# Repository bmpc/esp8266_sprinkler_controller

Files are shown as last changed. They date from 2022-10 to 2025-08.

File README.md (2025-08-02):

# ESP8266 sprinkler controller
 
A WiFi lawn irrigation controller using an [ESP-12F WiFi module](https://docs.ai-thinker.com/_media/esp8266/docs/esp-12f_product_specification_en.pdf) to drive up to 4 sprinkler stations.
 
The sprinkler stations can be controlled and programmed remotely using [Home Assistant](https://www.home-assistant.io/).
 
The ESP8266 board communicates with Home Assistant using an [MQTT](https://mqtt.org/) broker on the local WiFi network. The ESP8266 listens to events in order to turn on/off and to program the schedule for each sprinkler station.
 
The controller is powered by a 9V battery as this is also the voltage required to activate the solenoids for each sprinkler. Being a battery powered device, the efficiency of the circuit is very important. The ESP8266 needs to be in deep sleep as much as possible and only wake up for activating/deactivating sprinkler stations.
 
There is also an interface mode that can be activated explicitly using Home Assistant. In interface mode, the ESP8266 will not go into deep sleep and is always ready to receive commands to activate/deactivate stations and configure the system. This mode is useful if we need to test a specific sprinkler station or if we need to trigger the stations manually.
 
The controller is also equipped with a reset button which will force the system to wake up from deep sleep, and go into interface mode (if enabled).
 
<div style="text-align:center">
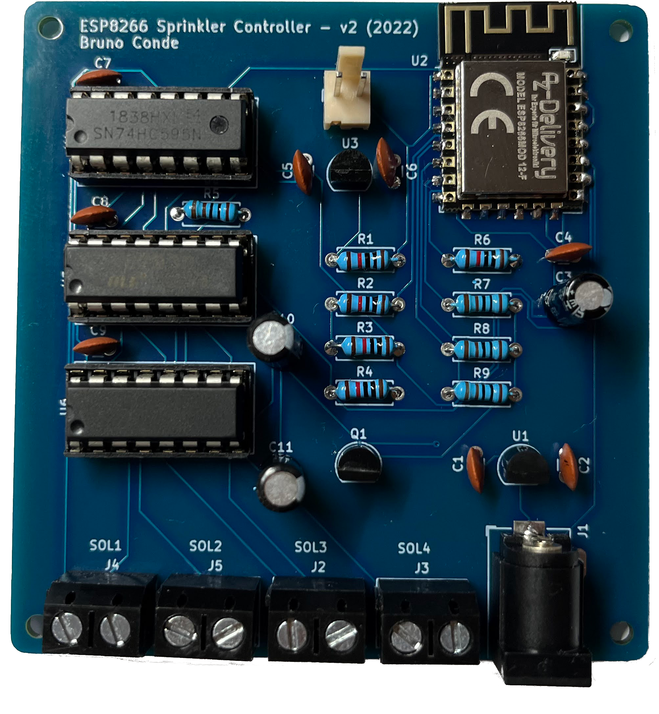
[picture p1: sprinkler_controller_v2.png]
Controller circuit
 
</div>
 
## MQTT Topics
 
### Subscribe
 
| Topic | Payload format | Payload example | Retained |
| --- | --- | --- | --- |
| `lawn-irrigation/station{x}/set` | `{"on","off"}\|{"duration in milliseconds"}` | `"on\|18000" ; "off"` | false |
| `lawn-irrigation/station{x}/config`  | `{"cron expression"}\|{"duration in milliseconds"}` | `"0 30 6 1-31/2 * *\|900"` | true |
| `lawn-irrigation/interface-mode/set` | `{"on","off"}` | `"on" ; "off"` | true |
| `lawn-irrigation/enabled/set` | `{"on","off"}` | `"on" ; "off"` | true |

### Publish
 
| Topic | Payload format | Payload example | Retained |
| --- | --- | --- | --- |
| `lawn-irrigation/station{x}/state` | `{"on","off"}` | `"on" ; "off"`  | false |
| `lawn-irrigation/interface-mode/state`  | `{"on","off"}` | `"on" ; "off"`  | false |
| `lawn-irrigation/log` |  `<string>` | `"log string"`  | true |
 
## How to configure Home Assistant
 
The esp8266 sprinkler controller is configured from [Home Assistant](https://www.home-assistant.io/) using [MQTT switches](https://www.home-assistant.io/integrations/switch.mqtt/) and input fields.
 
As an example, here is my lawn irrigation card within the Home Assistant dashboard. I have three sprinkler stations configured:
 
<div style="text-align:center">
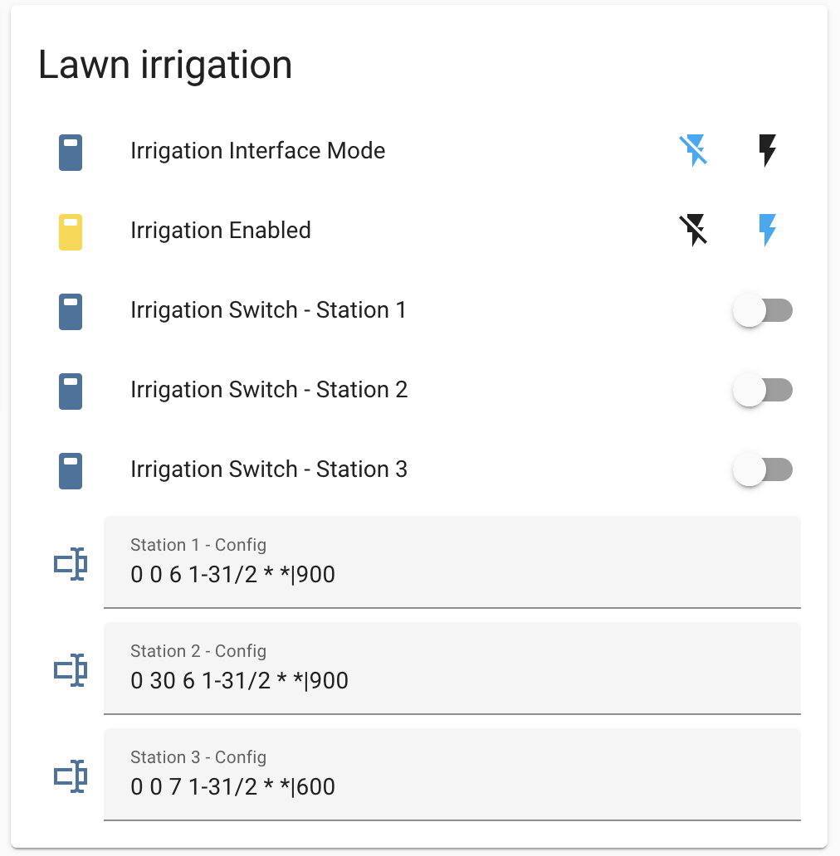
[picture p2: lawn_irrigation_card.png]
Home Assistant control card
 
</div>
 
Each station is controlled by a different MQTT switch. The switches automatically display the station state and are also used to trigger the stations manually (provided that the controller is in **interface mode**).
 
Besides the station controller switches and CRON inputs, there are two additional switches to toggle:
- the interface mode
- the irrigation itself.
 When the irrigation controller is in **interface mode**, the ESP8266 will not go into deep sleep and the user can toggle the stations directly.
 
The irrigation toggle switch can be used to skip the programmed schedule. As an example, it is possible to disable the irrigation if rain is forecast for the next 12 hours or is has rained in the last 12h.
 
Apart from the switches, [Input Text Fields](https://www.home-assistant.io/integrations/input_text/) are used to configure the CRON expression and duration for each station. An automation is also required so that an MQTT event is published whenever the text field changes.
 
If a station is activated due to the configured cron expression schedule, the respective switch will be updated automatically with the current status as an MQTT event is sent from the controller whenever there is a station event.
 
You can find an example on how to configure these MQTT switches and text fields on the HA examples included in this repository:
- [configuration.yaml](/ha/configuration.yaml)
- [automations.yaml](/ha/automations.yaml)

## Circuit
 
### Power
 
Because the solenoids that activate the sprinklers require 9V to activate, this circuit is powered by a 9V battery (two 9V batteries in parallel to be precise). A voltage regulator is used to step down from 9v to 5v so that we can power some 5v ICs in the circuit. The ESP-12F requires 3.3V. Therefore, another voltage regulator was added to step down from 5v to 3.3v. This is not ideal, as there are two voltage regulators but in this case we require 3 different voltages and it would not be practical to have multiple batteries for the same circuit.
 
### Latching solenoids and the L293D ICs
 
There are two L293D ICs in this circuit. These are Quadruple Half-H Drivers that are designed to provide bidirectional drive currents. The L293D is also designed to drive inductive loads such as solenoids and motors. These ICs allow us to drive the 9v power lines to the solenoid with a 3.3v logic signal provided by the ESP8266.
 
A latching solenoid uses an electrical current pulse or internal permanent magnet material to maintain a set position without the constant application of power. Latching solenoids (also known as bistable solenoids) have two standard positions; de-energized with the plunger fully extended and de-energized with the plunger held in position by permanent magnets.
 
Electrical polarity is vital to proper latching a solenoid. As current flows in one direction, adds to the pull of the permanent magnet. Sending a current through the coil field in the opposite direction cancels the magnet’s attraction and releases the plunger from the latched position.
 
These L293D ICs are required in order to control our latching solenoids because we need to provide opposite polarities depending on if we are activating or deactivating the solenoid.
 
Each L293D can control two solenoids. Hence two L293D ICs were used to drive a total of 4 solenoids/sprinkler stations.
 
### The lack of pins and the 8-bit shift register
 
Because the ESP12-F only provides 11 GPIO digital pins, an 8-bit shift register was included so we can have more digital lines to drive the four possible solenoids/stations.
 
### Power Efficiency
 
This is a very important topic as this circuit is powered with standard 9v batteries. Depending on the battery type, usually a 9v battery has a capacity of around 300 mAh.
We must guarantee that our circuit is as efficient as possible. Ideally, the standby current of the circuit should not exceed 50uA. In these conditions, I estimate around 300 to 400 days on double 9v batteries.
 
Operating normally, without any changes to improve the efficiency of the circuit, the average current is about 90mA to 130mA. This includes the ESP8266 making WiFi requests, the two L293D ICs, the 8-bit shift register, and added the voltage regulators.
 
If we put the ESP8266 in deep sleep mode, the current drops to about 50mA to 60mA. This is still too high. The culprits are the two L293D ICs which have a very high quiescent current of about 30mA each.
 
Hence, to reduce the quiescent current of the L293D ICs, the power is supplied to these ICs only when stations need to be activated/deactivated. To achieve this, a simple NPN transistor is used to turn off the shift register and both L293D ICs. This transistor is driven by the ESP8266.
 
Even though the L293D ICs are not connected to power in standby mode, some pins can have enough voltage to pull the ESP-12F GPIO15 line HIGH thus preventing the ESP-12F from booting. The solution was to add a diode between the GPIO15 enable line and the L293D chip.
 
After these improvements, I measured the standby current of the circuit to around **20uA**.

### RTC accuracy on the ESP8266 

The max deep sleep time of the ESP-12F is about 3 to 4 hours. Therefore, the ESP needs to wake up every 3 hours or so and get right back to sleep if no action is required (no station needs to be started or stopped).

Also, it turns out that the ESP8266 doesn't have a very precise RTC (Real Time Clock). On a 3 hour period, my ESP8266 RTC would drift ahead around 14 minutes. Without a more precise clock, and considering our use case, we can just go back to sleep for the remaining time. 
 
### Schematic
 
<div style="text-align:center">
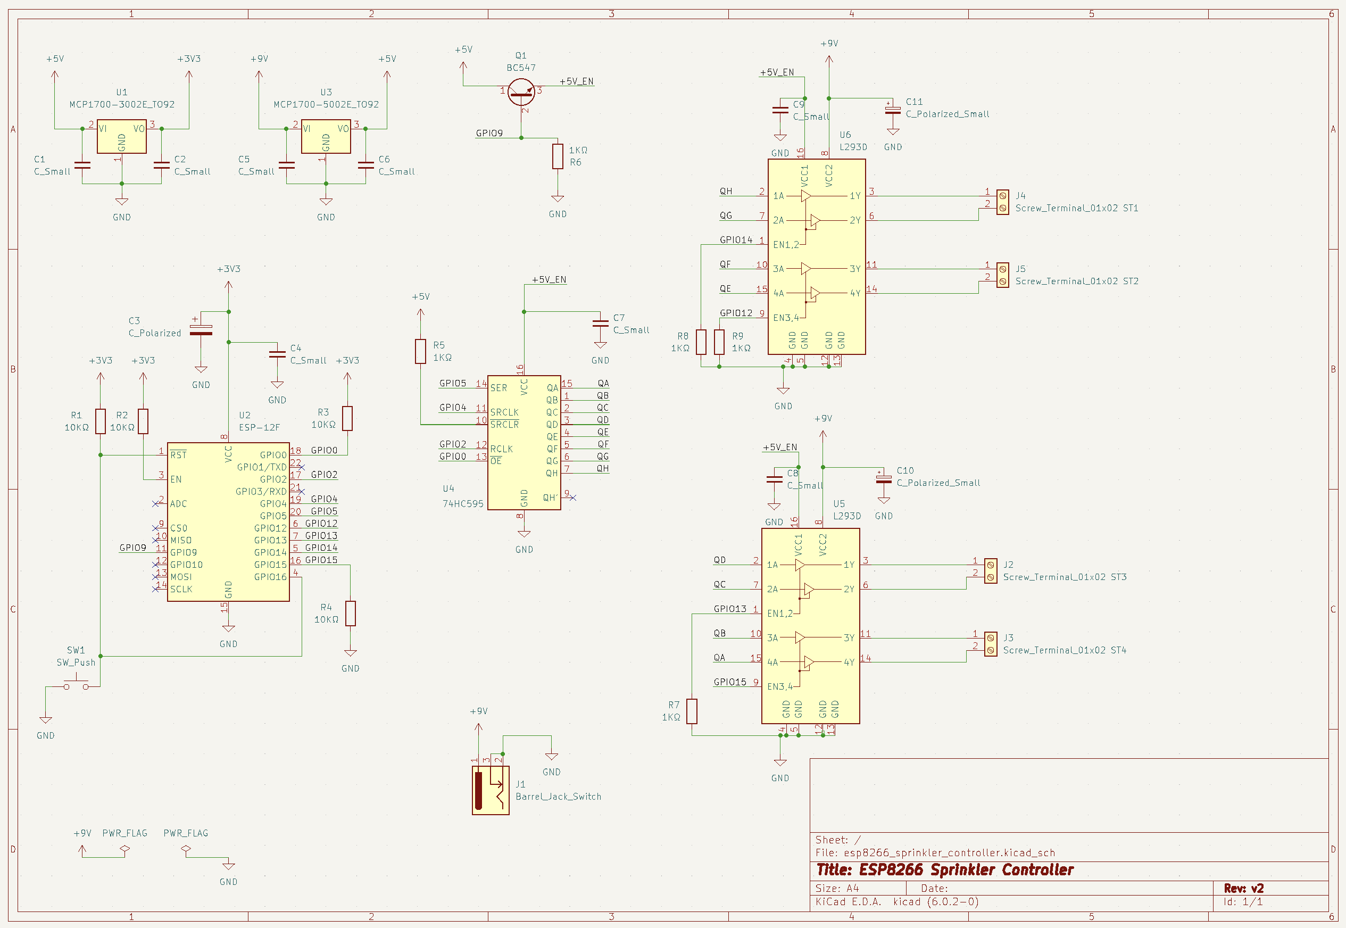
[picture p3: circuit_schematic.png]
Circuit Schematic
 
</div>
 
### BOM

| Part | Qty |
| --- | --- |
| ESP-12F (ESP8266) | x1  |
| L293D (Quadruple Half-H Drivers) | x2  |
| 74HC595 (8-bit shift register) | x1  |
| MCP1702-5002E/TO (voltage regulator) | x1  |
| MCP1702-3302E/TO (voltage regulator) | x1  |
| SS8050CBU (NPN transistor) | x1  |
| 100Ω resistor | x1  |
| 1k resistor | x4  |
| 10k resistor | x4  |
| 100 uF electrolytic capacitor | x2  |
| 10 uF electrolytic capacitor | x1  |
| 1 uF ceramic capacitor (104) | x8  |
| SD101A (Schottky Diode) | x1  |
| Switch (reset) | x1  |
| Barrel Jack Switch | x1  |
| Screw terminal | x4  |
| 9v battery | x2  |
| Rainbird solenoids | x3  |

## ESP8266 Project

The ESP8266 project was built using [Platform IO](https://docs.platformio.org/).

The platformio.ini file contains the default parameters to run the targets below. You can change this file or provide the parameters in the context of each `pio run <target>` command [(usage)](https://docs.platformio.org/en/latest/core/userguide/cmd_run.html#usage).

### Build

In order to compile and build the project you just need to run the following command.

`pio run build`

### Upload

You can upload the sketch using serial port or OTA (Over The Air).

The sketch is ready to receive (OTA) updates. In order to upload OTA, you need to set the `upload_port` parameter with the IP address or your ESP8266.
For serial upload, just se the `upload_port` parameter with the appropriate serial interface.

`pio run upload`

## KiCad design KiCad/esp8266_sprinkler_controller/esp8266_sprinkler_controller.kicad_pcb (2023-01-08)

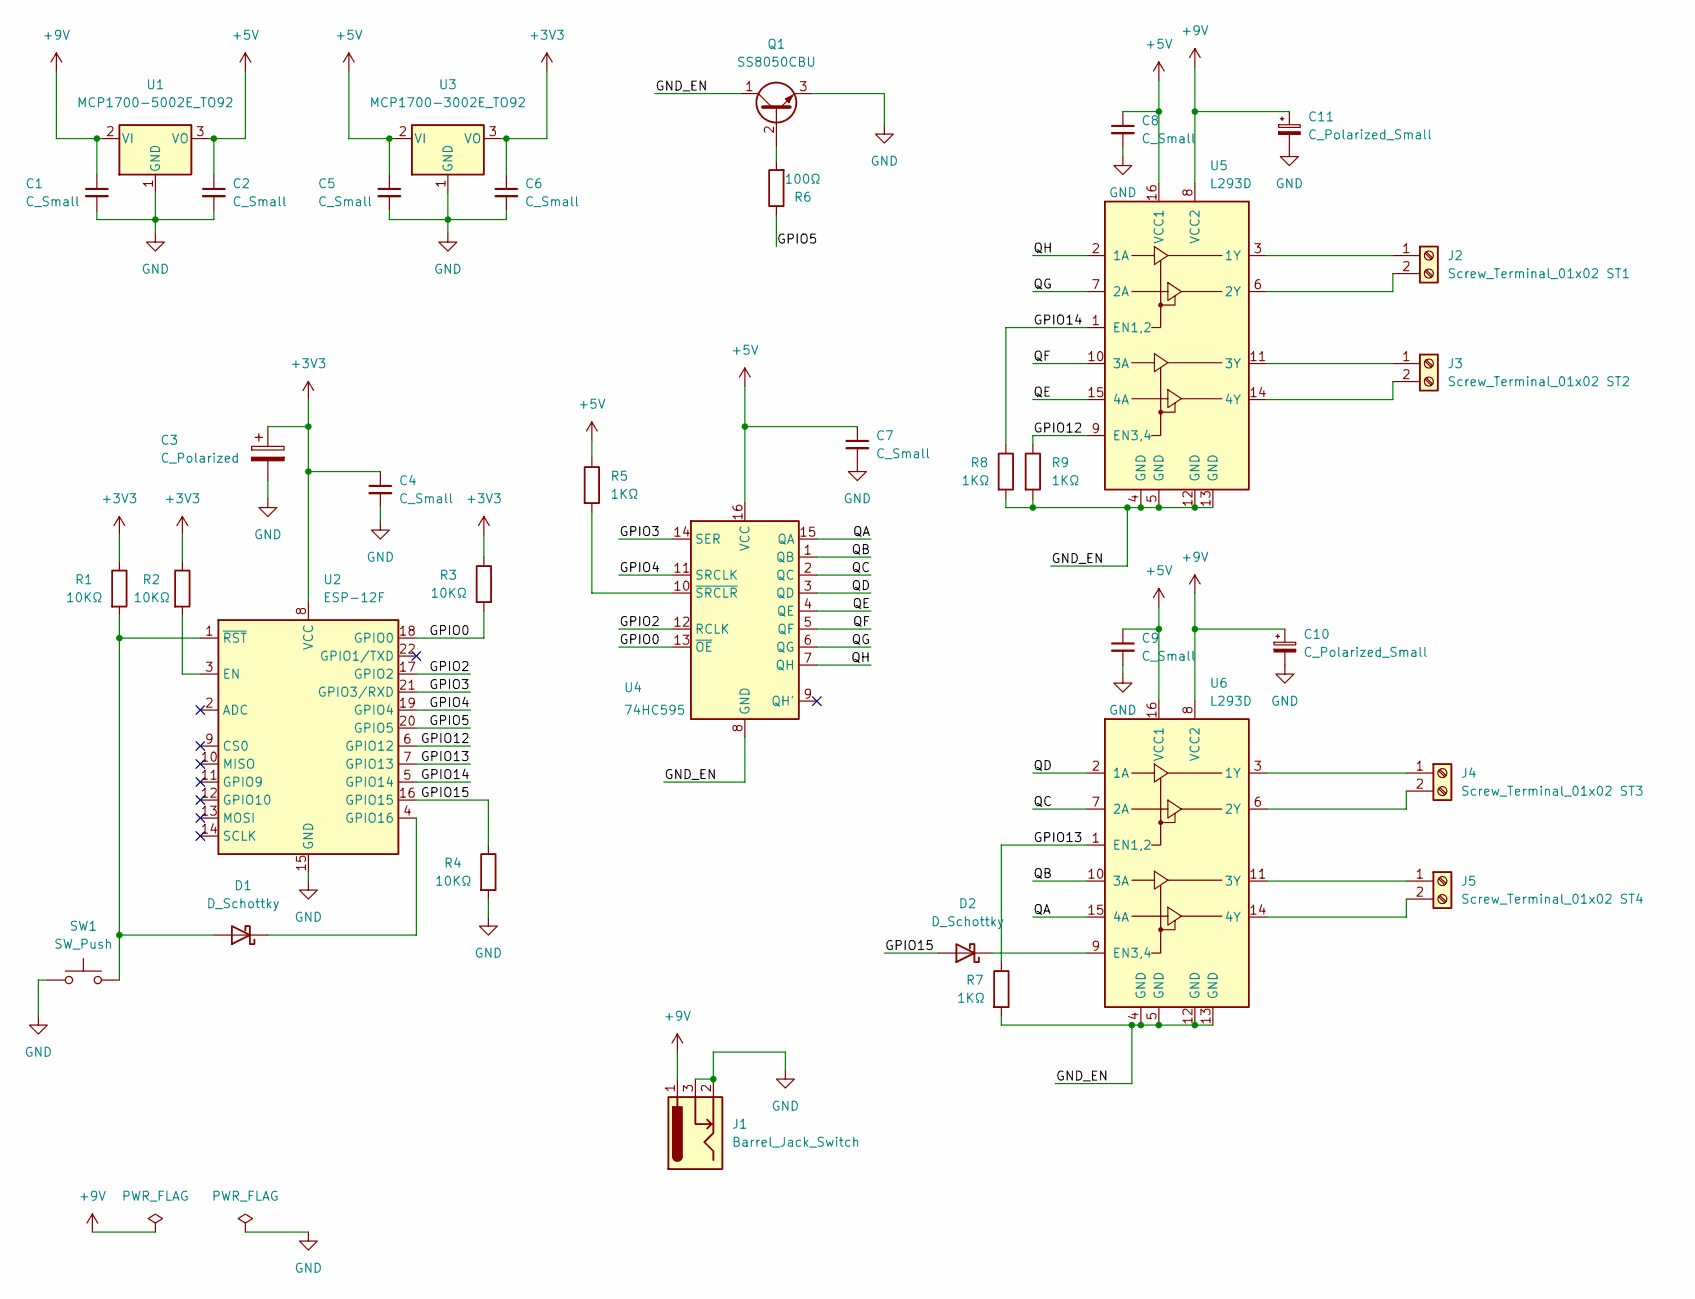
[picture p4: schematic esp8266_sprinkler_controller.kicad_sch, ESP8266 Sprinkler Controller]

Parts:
C1, C2, C4, C5, C6, C7, C8, C9: C_Small; C_Disc_D3.0mm_W1.6mm_P2.50mm
C3: C_Polarized; CP_Radial_D4.0mm_P2.00mm
C10, C11: C_Polarized_Small; CP_Radial_D4.0mm_P2.00mm
D1, D2: D_Schottky; D_A-405_P7.62mm_Horizontal
J1: Barrel_Jack_Switch; BarrelJack_Horizontal
J2: Screw_Terminal_01x02 ST1; TerminalBlock_bornier-2_P5.08mm
J3: Screw_Terminal_01x02 ST2; TerminalBlock_bornier-2_P5.08mm
J4: Screw_Terminal_01x02 ST3; TerminalBlock_bornier-2_P5.08mm
J5: Screw_Terminal_01x02 ST4; TerminalBlock_bornier-2_P5.08mm
Q1: SS8050CBU; TO-92
R1, R2, R3, R4: 10KΩ; R_Axial_DIN0207_L6.3mm_D2.5mm_P7.62mm_Horizontal
R5, R7, R8, R9: 1KΩ; R_Axial_DIN0207_L6.3mm_D2.5mm_P7.62mm_Horizontal
R6: 100Ω; R_Axial_DIN0207_L6.3mm_D2.5mm_P7.62mm_Horizontal
SW1: SW_Push; PinSocket_1x02_P2.54mm_Vertical
U1: MCP1700-5002E_TO92; TO-92
U2: ESP-12F; ESP-12E
U3: MCP1700-3002E_TO92; TO-92
U4: 74HC595; DIP-16_W7.62mm_Socket
U5, U6: L293D; DIP-16_W7.62mm_Socket

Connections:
+3V3: C3.1, C4.1, C6.1, R1.1, R2.1, R3.1, U2.8 (VCC), U3.3 (VO)
+5V: C2.1, C5.1, C7.1, C8.1, C9.1, R5.1, U1.3 (VO), U3.2 (VI), U4.16 (VCC), U5.16 (VCC1), U6.16 (VCC1)
+9V: C1.1, C10.1, C11.1, J1.1, U1.2 (VI), U5.8 (VCC2), U6.8 (VCC2)
/GND_EN: Q1.1 (C), R7.2, R8.2, R9.2, U4.8 (GND), U5.4 (GND), U5.5 (GND), U5.12 (GND), U5.13 (GND), U6.4 (GND), U6.5 (GND), U6.12 (GND), U6.13 (GND)
/GPIO0: R3.2, U2.18 (GPIO0), U4.13 (~OE)
/GPIO2: U2.17 (GPIO2), U4.12 (RCLK)
/GPIO3: U2.21 (GPIO3/RXD), U4.14 (SER)
/GPIO4: U2.19 (GPIO4), U4.11 (SRCLK)
/GPIO5: R6.1, U2.20 (GPIO5)
/GPIO12: R9.1, U2.6 (GPIO12), U5.9 (EN3,4)
/GPIO13: R7.1, U2.7 (GPIO13), U6.1 (EN1,2)
/GPIO14: R8.1, U2.5 (GPIO14), U5.1 (EN1,2)
/GPIO15: D2.2 (A), R4.1, U2.16 (GPIO15)
/QA: U4.15 (QA), U6.15 (4A)
/QB: U4.1 (QB), U6.10 (3A)
/QC: U4.2 (QC), U6.7 (2A)
/QD: U4.3 (QD), U6.2 (1A)
/QE: U4.4 (QE), U5.15 (4A)
/QF: U4.5 (QF), U5.10 (3A)
/QG: U4.6 (QG), U5.7 (2A)
/QH: U4.7 (QH), U5.2 (1A)
GND: C1.2, C2.2, C3.2, C4.2, C5.2, C6.2, C7.2, C8.2, C9.2, C10.2, C11.2, J1.2, J1.3, Q1.3 (E), R4.2, SW1.1, U1.1 (GND), U2.15 (GND), U3.1 (GND)
unnamed: D1.1 (K), U2.4 (GPIO16)
unnamed: D1.2 (A), R1.2, SW1.2, U2.1 (~RST)
unnamed: D2.1 (K), U6.9 (EN3,4)
unnamed: J2.1, U5.3 (1Y)
unnamed: J2.2, U5.6 (2Y)
unnamed: J3.1, U5.11 (3Y)
unnamed: J3.2, U5.14 (4Y)
unnamed: J4.1, U6.3 (1Y)
unnamed: J4.2, U6.6 (2Y)
unnamed: J5.1, U6.11 (3Y)
unnamed: J5.2, U6.14 (4Y)
unnamed: Q1.2 (B), R6.2
unnamed: R2.2, U2.3 (EN)
unnamed: R5.2, U4.10 (~SRCLR)

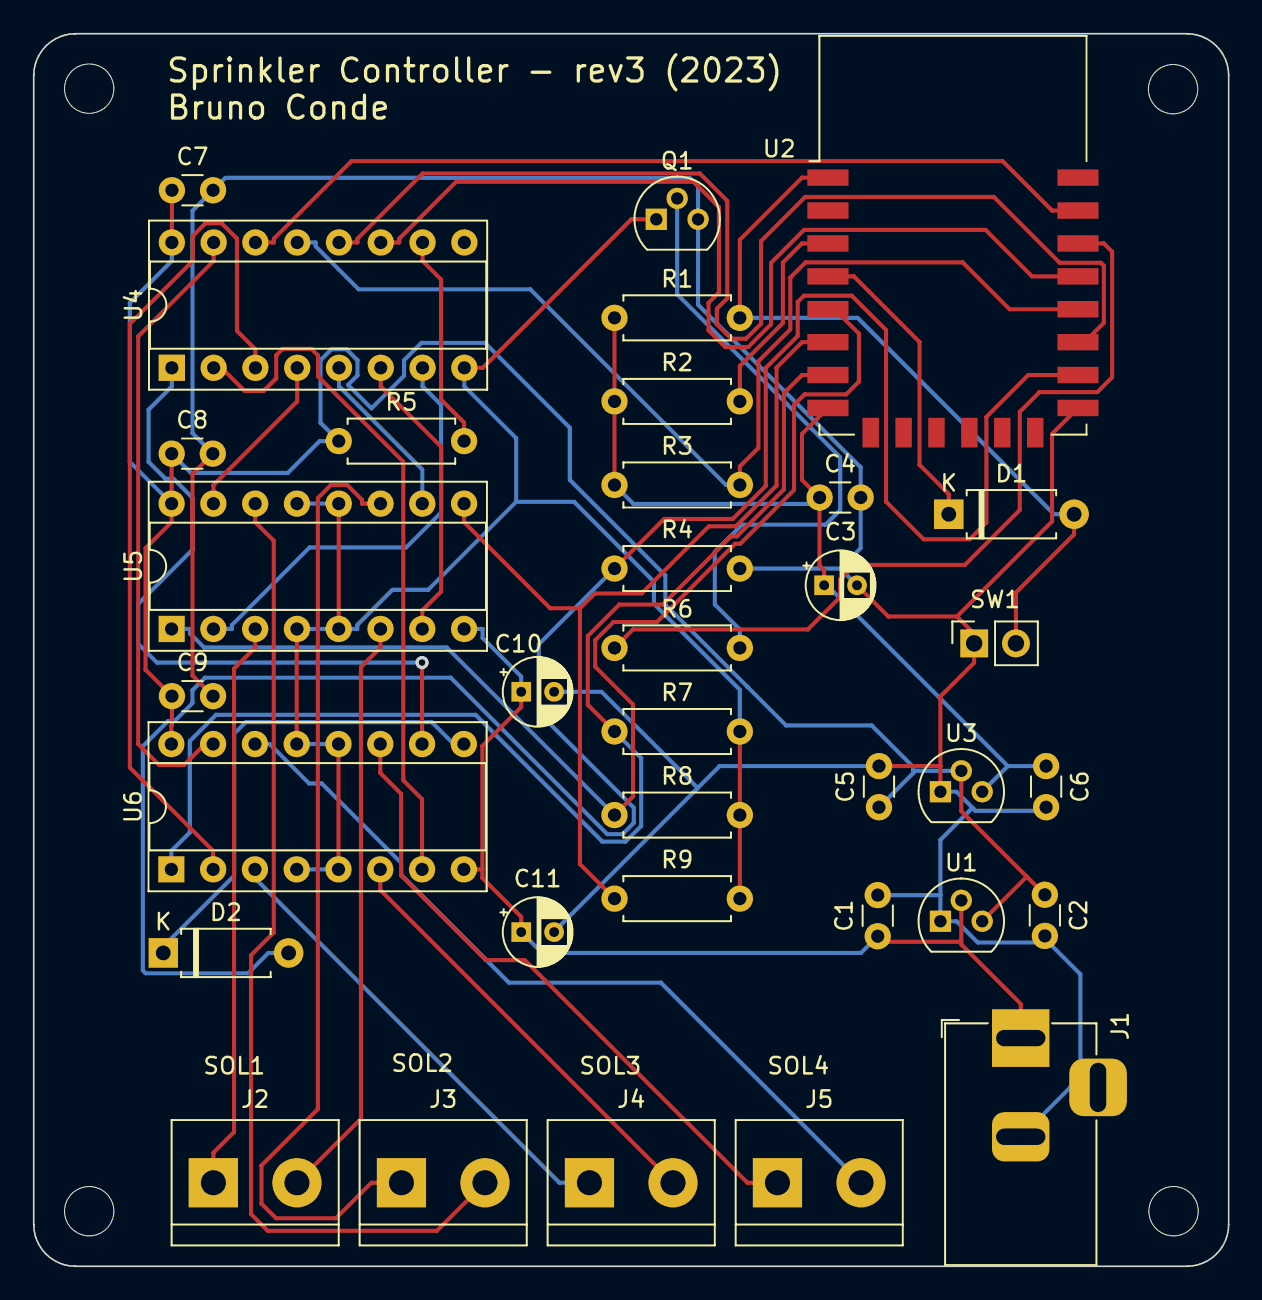
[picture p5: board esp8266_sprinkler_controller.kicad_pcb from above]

Board: 2 copper layers, 72.6 x 74.9 mm, 39 parts (0 on the bottom side), 36 nets.

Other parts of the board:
Hole1, Hole2, Hole3, Hole4: MountingHole_3mm

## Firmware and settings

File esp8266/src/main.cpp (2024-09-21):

/**
 * This is an esp8266 project to control a lawn irrigation system using
 * solanoids for each sprinkler station. It connects to an MQTT broker on the
 * local WiFi network so that it can listen for events to turn on/off each
 * sprinkler station on the irrigation system. 
 * 
 * The system has two functioning modes:
 *   1. Background - The default mode which triggers each station based on it's cron schedule.
 *   2. Interface  - An interactive mode where users can trigger specific stations from 
 *                   MQTT events (Usually used for ad-hoc watering or to test the spinklers).
 * 
 * The mode can be selected using an MQTT event. While on Background mode, the ESP8266 is 
 * in deep spleeping and a manual restart is required for the ESP8266 to restart and activate
 * the interface mode.
 * 
 * WARNING: While on interafce mode, the ESP8266 is always on. This will degrade the battery life much faster.
 * 
 * Stations are mutual exclusive. There can only be one station active at a time, which usually is the behavior of sprinkler irrigation systems.  
 * 
 * MQTT topics:
 *  Subsribe:
 *   - lawn-irrigation/station{x}/set     not retained -> payload: on|18000 ; off
 *   - lawn-irrigation/station{x}/config      retained -> payload: cron|18000
 *   - lawn-irrigation/interface-mode/set     retained -> payload: on ; off
 *   - lawn-irrigation/enabled/set            retained -> payload: on ; off
 * 
 *  Publish:
 *   - lawn-irrigation/station{x}/state
 *   - lawn-irrigation/interface-mode/state
 *   - lawn-irrigation/log
 *
 * @file main.cpp
 * @author Bruno Conde
 * @brief
 * @version 0.1
 * @date 2022-09-18
 *
 * @copyright Copyright (c) 2022
 *
 */

#include <Arduino.h>
#include <NTPClient.h>
#include <WiFiUdp.h>
#include <ArduinoOTA.h>

#include "mqttcli.h"
#include "stations.h"
#include "log.h"
#include "constants.h"

const int DEEP_SLEEP_THRESHOLD = 3 * 60 * 60; // 3 hours in seconds

using namespace sprinkler_controller;

StationController stctr;
WiFiUDP ntpUDP;
NTPClient time_client(ntpUDP);

void enter_deep_sleep() {
  // Find out the next event
  time_t now = time_client.getEpochTime();
  StationEvent ev = stctr.next_station_event();

  time_t sleep_duration = DEEP_SLEEP_THRESHOLD;
  if (ev.type != EventType::NOOP && ev.time > now) {
    time_t new_sleep_duration = ev.time - now;
    // The maximum deep sleep time is around 3 hours. This may vary due to temperature changes. 
    // ESP.deepSleepMax() provides the max deep sleep.
    // We wake up every 3 hours and go right back to sleep if no stations need to be started/stopped. 
    if (new_sleep_duration <= DEEP_SLEEP_THRESHOLD) {
      sleep_duration = new_sleep_duration;
    }

    char msg[200] = {0};
    ev.to_string(msg);
    report_log("[%lld] Next event: %s", now, msg);
  } else {
    // There isn't a next event to process
    report_log("[%lld] No next event found!", now);
  }

  report_log("[%lld] Entering deep sleep mode for '%lld' seconds... good night!", now, sleep_duration);

  mqttcli::disconnect();

  ESP.deepSleep(sleep_duration * 1000 * 1000); // convert from seconds to microseconds
}

void init_wifi() {
  delay(100);
  // We start by connecting to the WiFi network
  debug_printf("Connecting to %s\n", SSID);

  WiFi.setAutoConnect(true);
  WiFi.setAutoReconnect(true);

  WiFi.begin(SSID, PASSWORD);

  while (WiFi.status() != WL_CONNECTED) {
    debug_printf(".");
    delay(500);
  }

  randomSeed(micros());

  debug_printf("WiFi connected. IP address: %s\n", WiFi.localIP().toString().c_str());
}

void setup() {  
  setupSerial();

  init_wifi();
  time_client.begin();

  stctr.init(&time_client);

  if (!stctr.is_interface_mode()) {
    stctr.process_station_event();
    enter_deep_sleep();
  }

  ArduinoOTA.onStart([]() {
    String type;
    if (ArduinoOTA.getCommand() == U_FLASH) {
      type = "sketch";
    } else { // U_FS
      type = "filesystem";
    }

    // NOTE: if updating FS this would be the place to unmount FS using FS.end()
    debug_printf("Start updating %s\n", type);
  });
  ArduinoOTA.onEnd([]() {
    debug_printf("\nEnd");
  });
  ArduinoOTA.onProgress([](unsigned int progress, unsigned int total) {
    debug_printf("Progress: %u%%\r", (progress / (total / 100)));
  });
  ArduinoOTA.onError([](ota_error_t error) {
    debug_printf("Error[%u]: ", error);
    if (error == OTA_AUTH_ERROR) {
      debug_printf("Auth Failed");
    } else if (error == OTA_BEGIN_ERROR) {
      debug_printf("Begin Failed");
    } else if (error == OTA_CONNECT_ERROR) {
      debug_printf("Connect Failed");
    } else if (error == OTA_RECEIVE_ERROR) {
      debug_printf("Receive Failed");
    } else if (error == OTA_END_ERROR) {
      debug_printf("End Failed");
    }
    debug_printf("\n");
  });
  ArduinoOTA.begin();
}

void loop() {
  if (!stctr.is_interface_mode()) {
    debug_printf("Interface mode switched off.");
    // if we get here, this means that the interface mode was switched off
    stctr.check_stop_stations(true);
    enter_deep_sleep();
  }

  if (WiFi.status() != WL_CONNECTED) {
    Serial.println("WiFi disconnected. Reconnecting...");
    WiFi.reconnect();
    
    while (WiFi.status() != WL_CONNECTED) {
      debug_printf(".");
      delay(500);
    }

    stctr.init(&time_client);
  }

  ArduinoOTA.handle();

  stctr.loop();
  
}

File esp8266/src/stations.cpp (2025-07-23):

#include "stations.h"
#include "ccronexpr/ccronexpr.h"
#include "log.h"
#include <EEPROM.h>

namespace sprinkler_controller {

static uint8_t EEPROM_MARKER = 115;

static int EEPROM_SIZE = sizeof(EEPROM_MARKER) + sizeof(StationEvent) + (sizeof(Station) * NUM_STATIONS);

static uint64_t lastMillis = 0;

// topics to subscribe 
const char *SUBS_TOPICS[2] = {"lawn-irrigation/+/config","lawn-irrigation/+/set"};

// forward decl
static void enable_ics();
static void disable_ics();
static void set_stations_status(uint8_t status, uint8_t enable_pin);
static void report_status(const Station &station);
static time_t get_next_station_start(const char *cron, const time_t date);
static uint8_t get_station_id(const char *topic);
static int index_of(const char *str, const char *findstr);
static bool starts_with(const char* start_str, const char* str);
static void substr(const char s[], char sub[], int p, int l);
static void substr(const char s[], char sub[], int p);

void Station::start(time_t start, long dur = 0) {
  this->started = start;
  this->is_active = true;
  if (dur > 0) {
    this->active_duration = dur > MAX_DURATION ? MAX_DURATION : dur;
  } else {
    this->active_duration = this->config_duration;
  }

  uint8_t mask = 1 << (2 * (this->id - 1));
  set_stations_status(mask, enable_pin);
}

void Station::stop() {
  this->started = 0;
  this->is_active = false;
  this->active_duration = 0;

  uint8_t mask = 2 << (2 * (this->id - 1));
  set_stations_status(mask, enable_pin);
}

void Station::to_string(char* s) {
  sprintf(s, "Station[%d] { enable_pin: %d, is_active: %d, started: %lld, duration[active]: %ld, duration[config]: %ld, cron: '%s' }\n", id, enable_pin, is_active, started, active_duration, config_duration, cron);
}

void StationController::init(NTPClient *time_client) {
  debug_printf("Initializing...\n");

  m_time_client = time_client;

  EEPROM.begin(EEPROM_SIZE);

  digitalWrite(ENABLE_ICS_PIN, LOW);
  pinMode(ENABLE_ICS_PIN, OUTPUT);

  load();

  int retries = 5;
  while(!m_time_client->forceUpdate() && retries-- > 0);

  mqttcli::init([this](char *topic, byte *payload, uint32_t length) {
      debug_printf("MQTT Message arrived [%s]\n", topic);
  
      char payload_str[length + 1];
      memcpy(payload_str, payload, length);
      payload_str[length] = '\0';
  
      if (starts_with("lawn-irrigation/interface-mode/set", topic))  {
        process_topic_mode_set(payload_str, length); // retained message
      } else if (starts_with("lawn-irrigation/enabled/set", topic))  {
        process_topic_enabled_set(payload_str, length); // retained message
      } else if (starts_with("lawn-irrigation/station", topic))  {
        Station *station = get_station_from_topic(topic);
        if (station != NULL) {
          if (m_interface_mode && index_of(topic, "set") > 0) {
            process_topic_station_set(*station, payload_str, length);
          } else if (m_interface_mode && index_of(topic, "state") > 0) {
            process_topic_station_state(*station);
          } else if (index_of(topic, "config") > 0) {
            process_topic_station_config(*station, payload_str, length); // retained message
          }
        }
      }
    },
    SUBS_TOPICS, 
   2
  );

  // receive and process retained messages
  int loop_idx = 10;
  while (loop_idx-- > 0) {
    mqttcli::loop();
    delay(100);
  }

  time_t now = m_time_client->getEpochTime();
  report_log("### Started at: '%lld'. Epoch Time Retries: '%d' ###\n", now, 5 - retries);

  print_state();

  debug_printf("MQTT init complete.\n");
}

void StationController::loop() {
  m_time_client->update();
  mqttcli::loop();

  // process station events every 30 seconds
  if (millis() - lastMillis >= 30*1000UL) {
      lastMillis = millis();

      process_station_event();
      next_station_event();
  }
}

void StationController::set_interface_mode(bool mode) {
  m_interface_mode = mode;

  save();

  report_interface_mode_state();
}

// TOPIC format: lawn-irrigation/station#/set
Station *StationController::get_station_from_topic(const char* topic) {
  uint8_t station_id = get_station_id(topic);
  if (station_id > 0 && station_id <= NUM_STATIONS) {
    return &(m_stations[station_id - 1]);
  }

  return NULL;
}

void StationController::check_stop_stations(bool force) {
  for (int i = 0; i < NUM_STATIONS; i++) {
    Station &station = this->m_stations[i];
    time_t now = m_time_client->getEpochTime();
    if (station.is_active == true) {
      if (force || ((now - station.started) > station.active_duration)) {
        report_log("[%lld] Stopping station %d. Started = %lld, Duration[active] = %ld, Elapsed = %lld, Forced = %d", now, station.id, station.started, station.active_duration, now - station.started, force);
        
        station.stop();

        report_status(station);
      }
    }
  }
}

StationEvent StationController::next_station_event() {
  StationEvent next_event;

  for (int i = 0; i < NUM_STATIONS; i++) {
    Station &station = m_stations[i];

    if (station.is_active == true) {
      time_t t = station.started + station.active_duration;
      if (next_event.time == 0 || next_event.time > t) {
        next_event.id = station.id;
        next_event.time = t;
        next_event.type = EventType::STOP;
      }
    } else {
      if (strlen(station.cron) > 0) {
        time_t t = get_next_station_start(station.cron, m_time_client->getEpochTime());
        if (next_event.time == 0 || next_event.time > t) {
          next_event.id = station.id;
          next_event.time = t;
          next_event.duration = station.config_duration;
          next_event.type = EventType::START;
        }
      }
    }
  }

  m_station_event = next_event;

  save();

  char msg[100];
  next_event.to_string(msg);
  debug_printf("Next Station Event: %s\n", msg);

  return next_event;
}
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

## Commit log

2022-10-01 New version that properly handles latching solenoids using the L293 half-H drivers IC; Kicad schematic for circuit; New interaction with Home Assistant; ESP8266 Deep Sleep
    [esp8266_sprinkler_controller-B_Cu.gbl, esp8266_sprinkler_controller-B_Mask.gbs, esp8266_sprinkler_controller-B_Paste.gbp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]
2022-10-24 Researching a way to use less power when the circuit is in deep sleep; Updated Kicad schematic and pcb design
    [esp8266_sprinkler_controller.dsn, esp8266_sprinkler_controller.kicad_pcb, esp8266_sprinkler_controller.kicad_sch]
2022-11-22 Refactor esp8266 code; New Kicad schematic version (v2.0) to make the circuit battery efficient
    [esp8266_sprinkler_controller-B_Cu.gbl, esp8266_sprinkler_controller-B_Mask.gbs, esp8266_sprinkler_controller-B_Paste.gbp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]
2022-11-22 Removed old circuit image
2023-01-08 KiCad: Revision 3 of schematic abdnd PCB. Solved a couple of circuit problems: - Added a Schottky Diode between the reset line and GPIO16 so this pin is not shorted when the reset button is pressed. 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
    ESP8266: Force a loop call to the MQTT broker when interface_mode is not active
    as MQTT messages were not being published correctly because the ESP8266 would
    go into deep sleep before it finished processing the messages.
    [esp8266_sprinkler_controller.dsn, esp8266_sprinkler_controller.kicad_pcb, esp8266_sprinkler_controller.kicad_sch]
2024-06-02 Fixed small bugs; Added logs; Removed interface mode when there is no next event
    [main.cpp, stations.cpp, stations.h]
2024-07-03 Fixed invalid logic when activating/deactivating stations
    [stations.cpp]
2024-08-10 Stations will now be enabled/disabled based on the schedule even if interface mode is ON. In other words, we can now use the spinkler controller always connected to power, without the need to sleep t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
2024-08-13 Fixed bug where the station duration was being set to zero when it stops
    [stations.cpp]
2024-08-18 Fixed bug where the scheduled duration of a stations was being mixed with the active duration of a station
    [stations.cpp, stations.h]
2025-07-23 Solved a bug where mqtt topics were not being subscribed after an MQTT reconnect
    [stations.cpp]
